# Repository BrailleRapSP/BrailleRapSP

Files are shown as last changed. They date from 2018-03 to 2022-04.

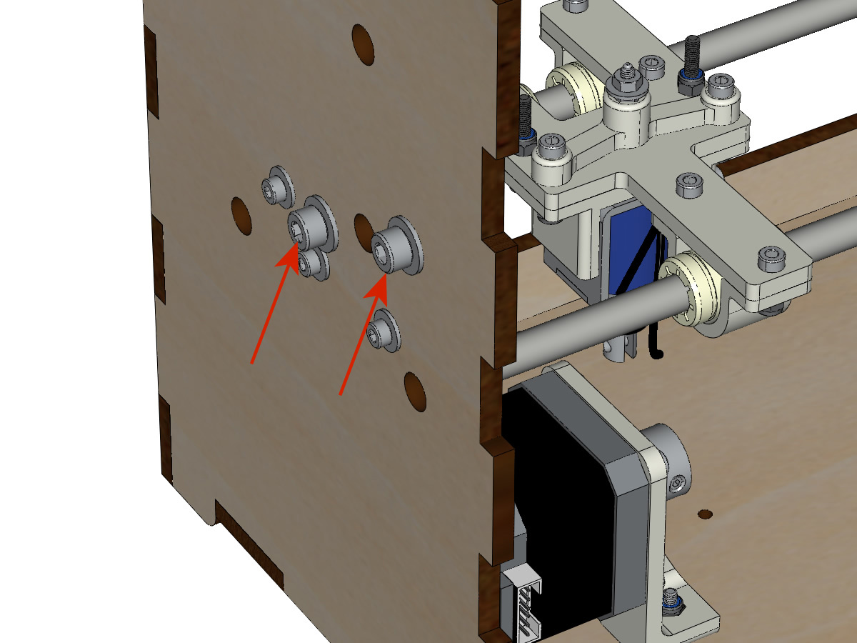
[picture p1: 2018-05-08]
docs/IMG/BrailleRAP-V5.68.jpg

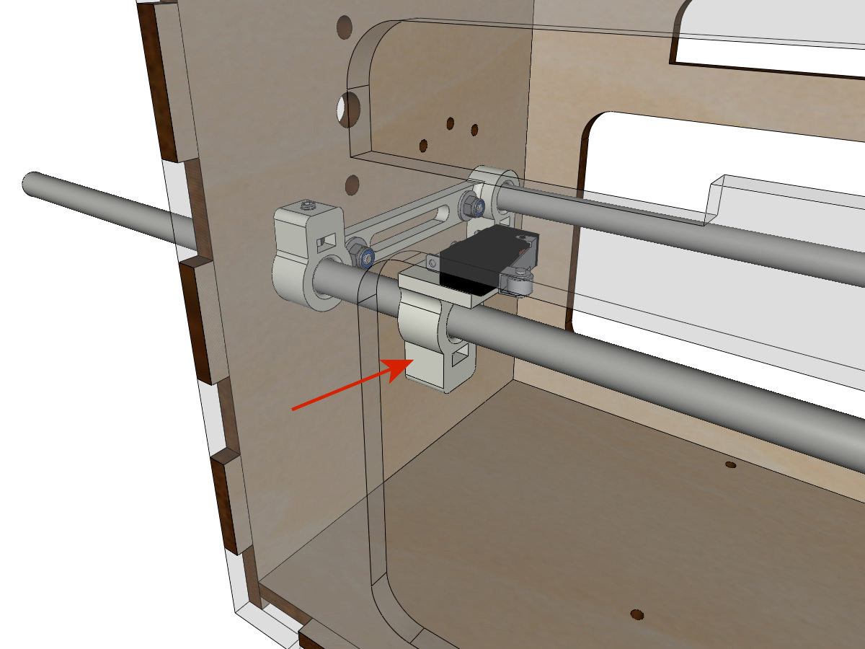
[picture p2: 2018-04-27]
docs/IMG/BrailleRAP-V5.52.jpg

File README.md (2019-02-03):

# BrailleRapSP

Embosseuse Braille Open Source

La documentation complete est disponible ici http://braillerapsp.readthedocs.io/fr/latest/index.html

voir egalement http://www.braillerap.com

==========================================================================

Open Source Braille embosser

the full documentation is available here https://braillerapsp-en.readthedocs.io/en/latest/index.html

BrailleRapSP also have a website http://www.braillerap.com

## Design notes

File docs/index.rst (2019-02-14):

.. BrailleRap-SP documentation master file, created by
   sphinx-quickstart on Mon Mar  5 11:31:40 2018.
   You can adapt this file completely to your liking, but it should at least
   contain the root `toctree` directive.

Bienvenue sur la documentation BrailleRAP-SP
============================================

.. image :: ./IMG/brailleRAP_couv.jpg 
  :width: 400px
  :align: center

Contenu:

.. toctree::
   :maxdepth: 3

   history
   licence
   bom
   assemblage
   marlin
   firstembossingpage
   
.. index:: history, licence, bom, marlin, assemblage, firstembossingpage

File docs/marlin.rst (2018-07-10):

Marlin Firmware pour cartes Ramps ou compatibles
================================================

.. Note:: Le firmware Marlin est utilisé pour contrôler l'embosseuse Braille. Nous utilisons la configuration CNC pour contrôler l'électro-aimant avec les commandes associées au moteur de CNC / stylo / laser (GCODE M3 et M4)

Configuration Marlin
-------------------

in configuration.h 

Motherboard configuration ::

   #ifndef MOTHERBOARD
     //#define MOTHERBOARD BOARD_RAMPS_14_EFB
     #define MOTHERBOARD BOARD_RAMPS_14_SF
   #endif

Spindle / laser / pen configuration ::

   // BRAILLE RAP CONFIG
   #define SPINDLE_LASER_ENABLE
   #define SPINDLE_LASER_ENABLE_PIN  RAMPS_D8_PIN      // !!! for BED MOSFET
   #define SPINDLE_LASER_PWM_PIN     RAMPS_D10_PIN     // !!! for E0 MOSFET 
   #define SPINDLE_DIR_PIN           5                 // pin servo

Endstop configuration ::

   // Mechanical endstop with COM to ground and NC to Signal uses "false" here (most common setup).
   #define X_MIN_ENDSTOP_INVERTING false // set to true to invert the logic of the endstop.
   #define Y_MIN_ENDSTOP_INVERTING false // set to true to invert the logic of the endstop.
   #define Z_MIN_ENDSTOP_INVERTING false // set to true to invert the logic of the endstop.
   #define X_MAX_ENDSTOP_INVERTING false // set to true to invert the logic of the endstop.
   #define Y_MAX_ENDSTOP_INVERTING false // set to true to invert the logic of the endstop.
   #define Z_MAX_ENDSTOP_INVERTING false // set to true to invert the logic of the endstop.
   #define Z_MIN_PROBE_ENDSTOP_INVERTING false // set to true to invert the logic of the probe.

Motor step / mm ::

   #define DEFAULT_AXIS_STEPS_PER_UNIT   { 80, 46, 4000, 500 }

Max feedrate ::

   #define DEFAULT_MAX_FEEDRATE          { 300, 300, 5, 25 }

Acceleration ::

   #define DEFAULT_MAX_ACCELERATION      { 1500, 1500, 100, 10000 }

   #define DEFAULT_ACCELERATION          1500    // X, Y, Z and E acceleration for printing moves
   #define DEFAULT_RETRACT_ACCELERATION  1500    // E acceleration for retracts
   #define DEFAULT_TRAVEL_ACCELERATION   1500    // X, Y, Z acceleration for travel (non printing) moves

Jerk ::

   #define DEFAULT_XJERK                 5.0
   #define DEFAULT_YJERK                 5.0
   #define DEFAULT_ZJERK                 0.3
   #define DEFAULT_EJERK                 5.0

Dans la version présente sur le github du projet BrailleRap-SP, d'autres fichiers ont été modifiés pour gérer l'alimentation du papier avec le fin de course de l'axe Y.

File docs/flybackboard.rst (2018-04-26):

PCB diode de roue libre 
=======================

Introduction
------------

.. Important:: Nous utilisons le connecteur de bed pour contrôler l'electro-aimant (comme on pourrait le faire avec une tête de CNC piloter par une carte RAMPS). Les electro-aimant sont des composants disposant d'une bobine, vous **devez absolument** utiliser une diode de roue libre entre le connecteur de Bed et le connecteur de l'electro-aimant pour protéger la carte RAMPS.

Schemas
-------

.. image :: ./IMG/flyback.png
    :align: center
	
.. image :: ./IMG/flyback_schema.png
    :align: center

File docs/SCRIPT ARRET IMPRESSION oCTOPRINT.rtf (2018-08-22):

M104 S0 ;extruder heater off
M140 S0 ;heated bed heater off (if you have it)
G91 ;relative positioning
G1 E-1 F300 ;retract the filament a bit before lifting the nozzle, to release some of the pressure
G1 Z+0.5 E-5 X-20 Y-20 F5000 ;move Z up a bit and retract filament even more
G28 X0 Y0 ;move X/Y to min endstops, so the head is out of the way
M84 ;steppers off
G90 ;absolute positioning
M107 ;start with the fan off
;{profile_string}

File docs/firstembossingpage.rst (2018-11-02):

Embosser votre première page de Braille
=======================================

BrailleRapSP est est machine qui se pilote en G-CODE, pour embosser du braille il faut tout d'abord traduire le texte en Braille.
Il existe 2 solutions pour traduire le Braille :
L'application BrailleRap en ligne https://crocsg.github.io/BrailleRap/
L'application NatBraille http://natbraille.free.fr 

Utilisation de l'application BrailleRap
---------------------------------------

Aller sur la page https://crocsg.github.io/BrailleRap/

.. image :: ./IMG/braillerapapp.png
       :align: center
Entrer votre texte à l'endroit indiqué, et télécharger ensuite le fichier GCODE contenant les instructions pour l'embosseuse

.. image :: ./IMG/braillerapapp_download.png
       :align: center

Vous pouvez ensuite utiliser un logiciel comme **cura** ou **pronterface** pour envoyer le fichier GCODE à l'imprimante

Configuration NatBraille
------------------------

Compiler les programmes dans le repertoire NatBrailleTools du projet

Dans les options générales NatBraille, utiliser **TbFr2007** pour la table braille, Encodage document noir **Automtique**, Encodage document braille **Windows1252**

.. image :: ./IMG/natbraille.png
       :align: center

Dans les options d'embossage, utiliser **TbFr2007** pour la table braille pour l'embossage

Activer l'option **utiliser une commande systeme pour l'embossage**

le paramêtre  pour commande d'impression est : **java -jar d:\\usr\\home\\logger\\BrailleLogger.jar $f | java -jar d:\\usr\\home\\logger\\gcodestreamer.jar COM4 250000**
en modifiant eventuellement les repertoires d'installation des programmes
COM4 est le port serie utilisé pour communiquer avec l'imprimante

.. image :: ./IMG/natbrailleembossig.png
       :align: center

Dans les options de mise en page, indiquer 31 et 26 dans le nombre de caracter par ligne et le nombre de lignes par page

.. image :: ./IMG/natbraille_page.png
       :align: center

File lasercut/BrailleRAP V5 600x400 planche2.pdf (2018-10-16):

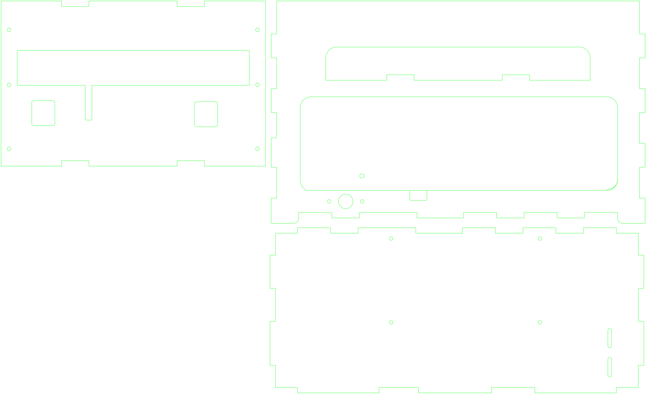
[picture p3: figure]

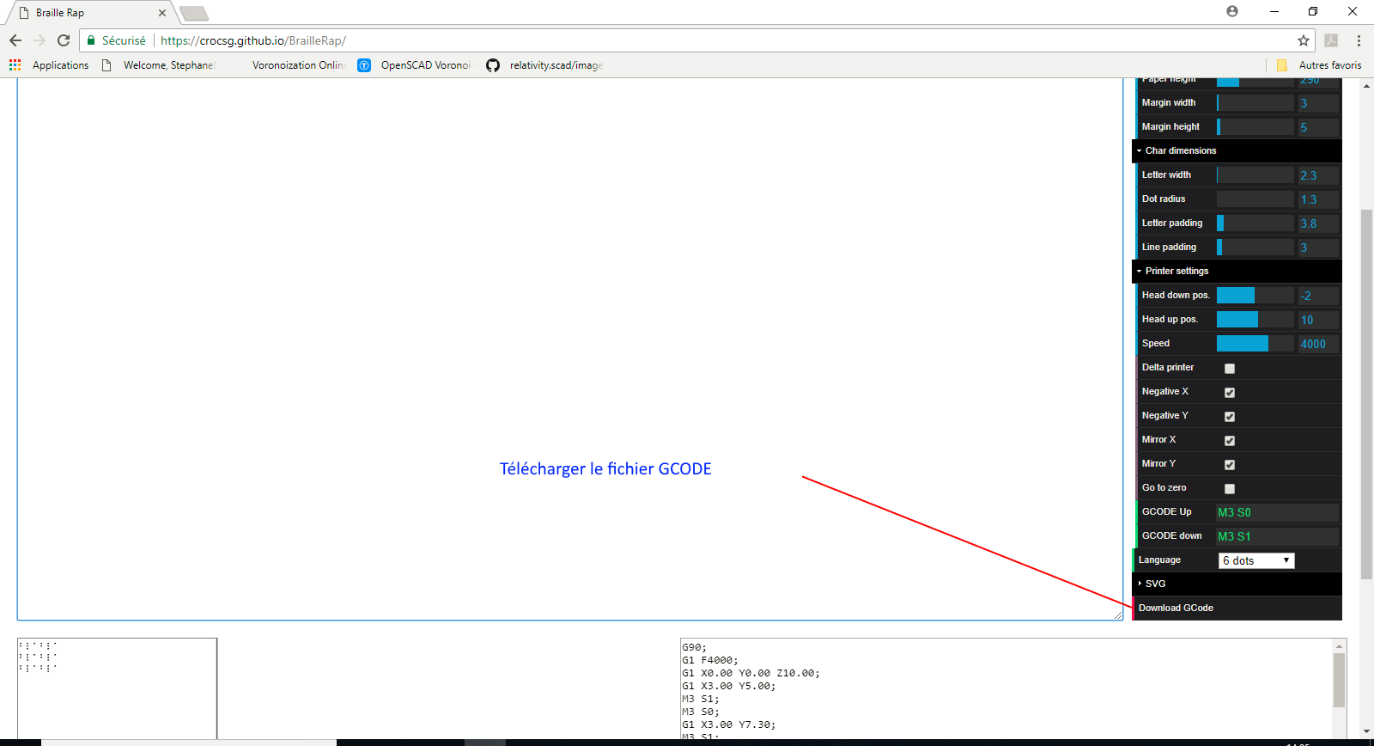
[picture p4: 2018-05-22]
docs/IMG/braillerapapp_download.png

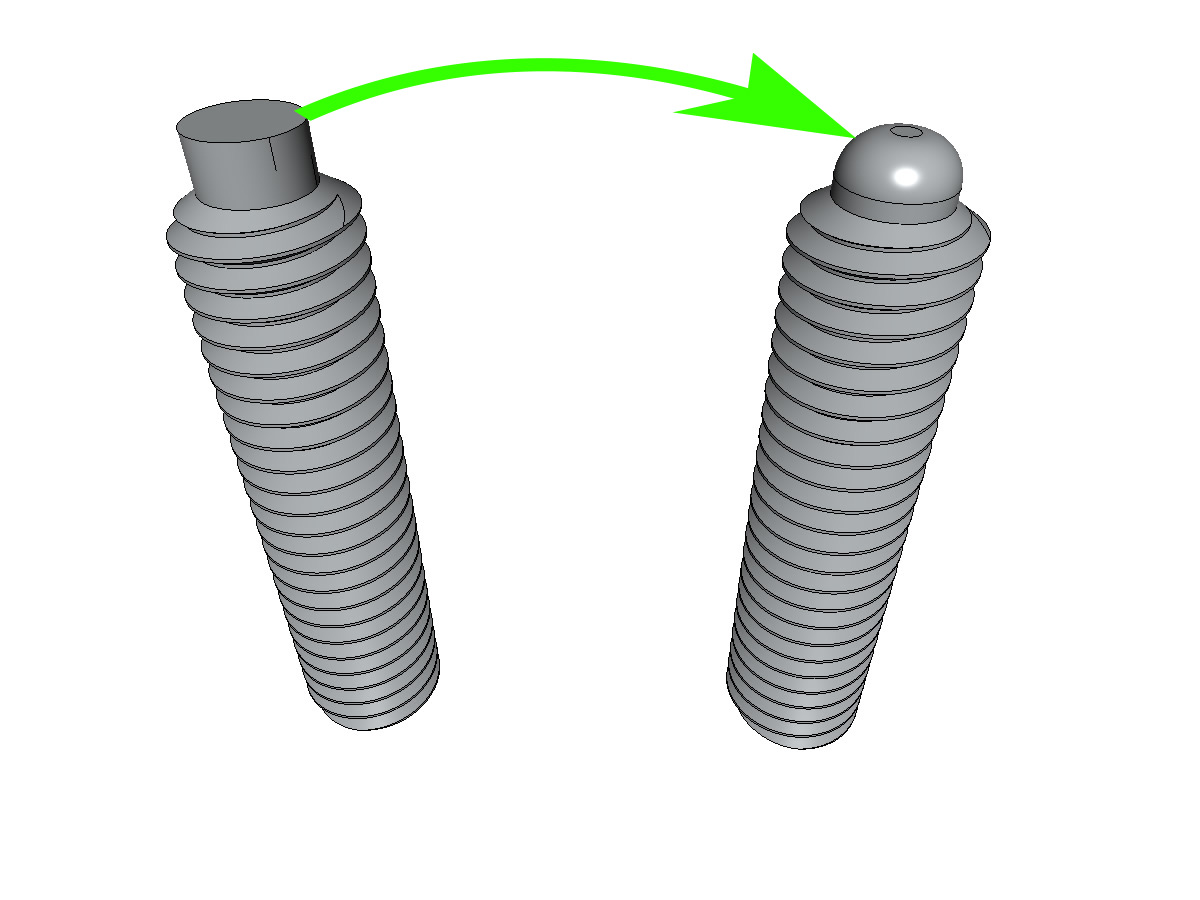
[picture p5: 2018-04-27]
docs/IMG/BrailleRAP-V5.56.jpg

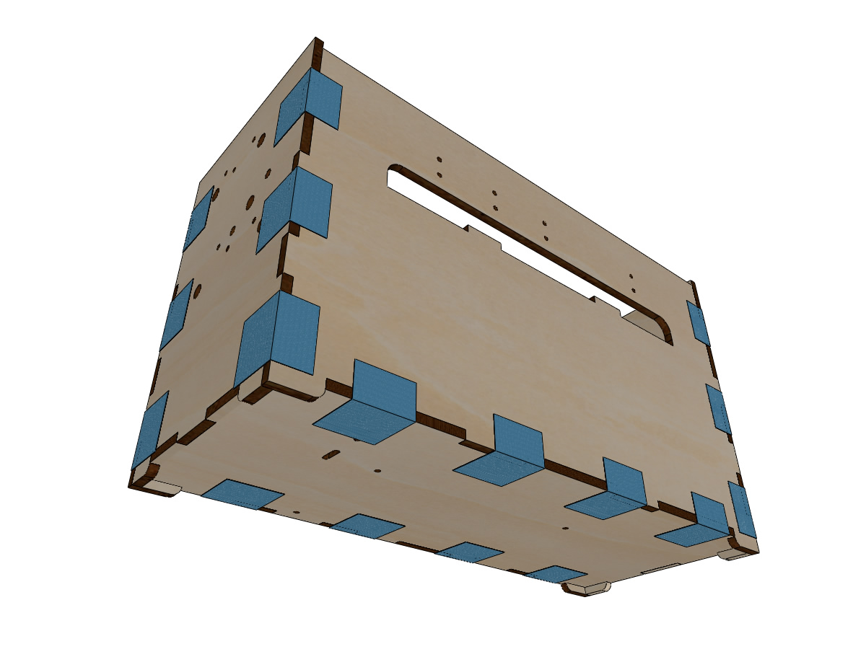
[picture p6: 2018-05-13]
docs/IMG/BrailleRAP-V5.01.jpg

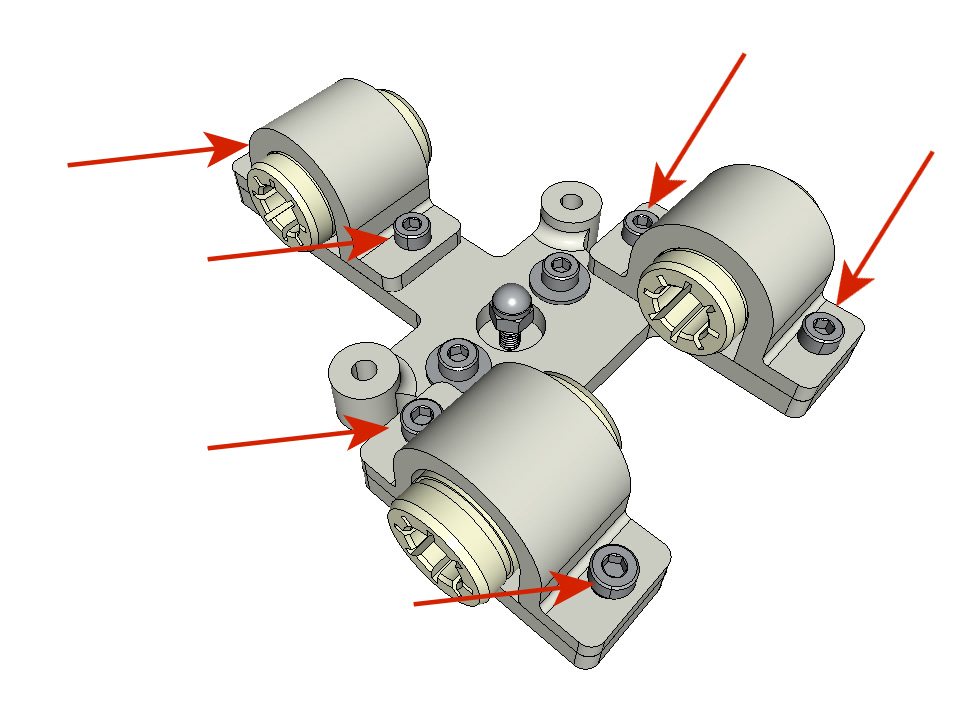
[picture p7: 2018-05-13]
docs/IMG/BrailleRAP-V5.85.jpg

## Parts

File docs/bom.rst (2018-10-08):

Liste du matériel
================

Découpe laser
-------------
2 planches de contreplaqué 5mm en 600mm x 400mm.

Les fichiers au format dxf sont disponibles ici : https://github.com/BrailleRapSP/BrailleRapSP/tree/master/lasercut

Pièces imprimées
-------------
Toutes les pièces sont imprimées en ABS, 50% de remplissage, 3 périmètres extérieurs. Nous utilisons le filament eSun ABS Natural.

Ajouter le lien pour le téléchargement de STL

Pièces mécaniques
----------------

=== =========================================
Qty Type
=== =========================================
4   Rail de guidage linéaire ( diamètre 8mm ) 330 mm length
1   Rail de guidage linéaire ( diamètre 8mm ) 365 mm length
1   Rail de guidage linéaire ( diamètre 8mm ) *100 mm* length

6   RJ4JP-01-08 palier linéaire Polymer  

3   GT2 poulie 20 dents pour axe 8mm    
2   GT2 poulie libre 20 dents axe 3mm (avec roulement à billes)

2   KP08  pallier horizontal pour rail linéaire 8mm 
2   KFL08 pallier vertical pour rail linéaire 8mm 

1   Accouplement d'axe 5mm/8mm

2   Nema 17 40 N/cm avec câble

1   Courroie GT2 fermée 200 mm
2   630 mm de courroie GT2

2   Joints torique 15.1 mm diamètre intérieur 20.5 mm de diamètre extérieur (15.1 x 20.5 x 2.7)
...
=== =========================================

Electronique
------------------

=== =========================================
Qty Type
=== =========================================
1   MKS GEN 1.4 ou carte compatible Ramps 1.4 
2   drivers DRV8825 avec radiateur
1   Electro-aimant *tau-826* 12V 2A
1   1N4004  diode de roue libre ou equivalent (12V 2A)
1   Embase Alimentation jack 2.5
1   Alimentation 12v 6A 
=== =========================================

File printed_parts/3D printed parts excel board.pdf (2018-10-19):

SCROLL_wheel | 2
KP08_support | 2
IGUS_housing | 6

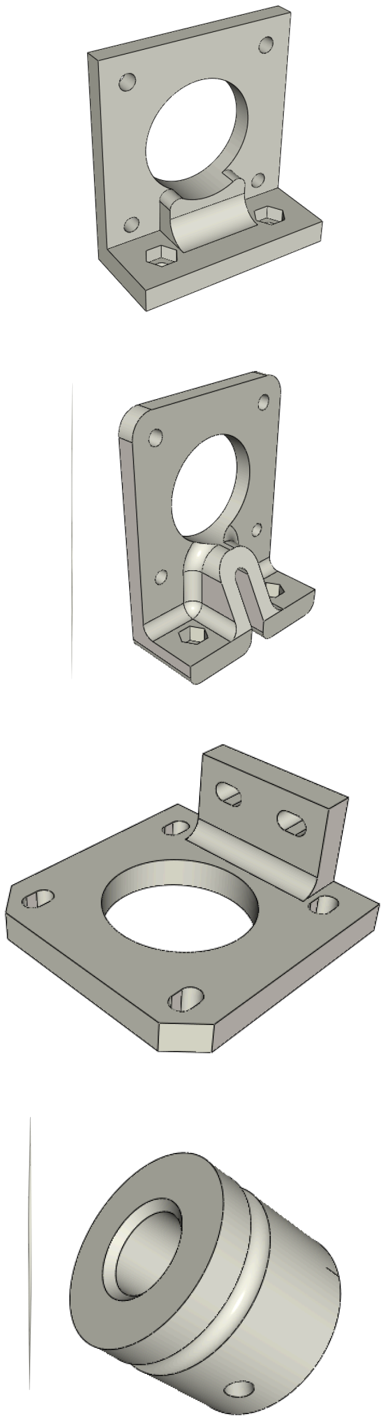
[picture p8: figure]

YMOTOR_support_220 | 1 | for 220mm GT2 timing belt
YMOTOR_support_200 | 1 | for 200mm GT2 timing belt
XMOTOR_support | 1
ROLL_joint | 2
BOTTOM_trolley | 1

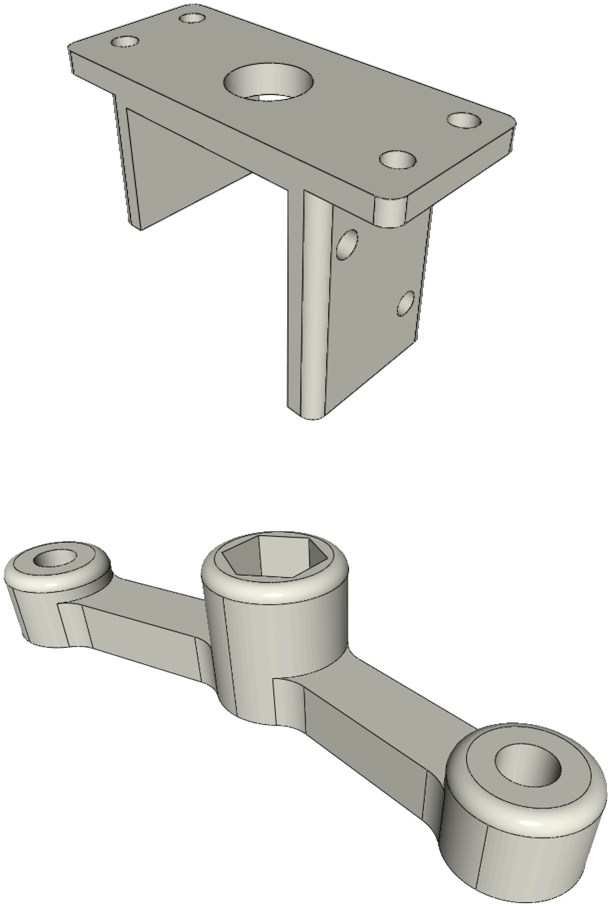
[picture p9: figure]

ELECTRO_MAGNET_housing | 1
ELECTRO_MAGNET_guide | 1
TOP_trolley | 1

FEMALE_shape | 1
TOP_AXIS_left | 1

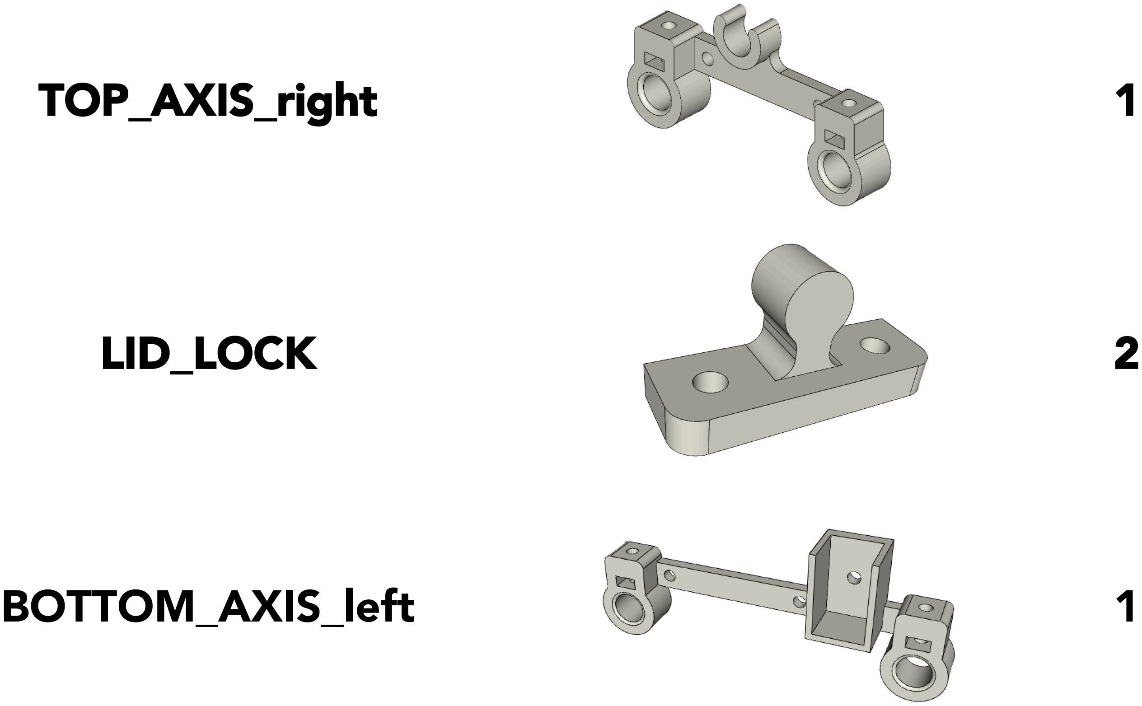
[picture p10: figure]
TOP_AXIS_right; LID_LOCK; BOTTOM_AXIS_left

BOTTOM_AXIS_right | 1
DRIVEN_PULLEY_housing | 2
PAPER_GUIDE_left | 1
PAPER_GUIDE_right | 1
SWITCH_Y_support | 1
PAPER_raiser | 2

SWITCH_X_support | 1
CLIPBOARD | 2
CLIPBOARD_WHEEL | 2
POWER_plate | 1

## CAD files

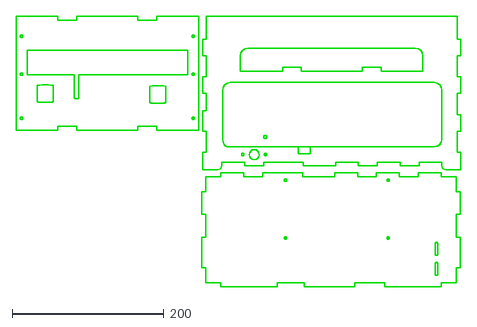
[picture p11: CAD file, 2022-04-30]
lasercut/BrailleRAP V5 600x400 planche2-r14.dxf
585.6 x 355.9

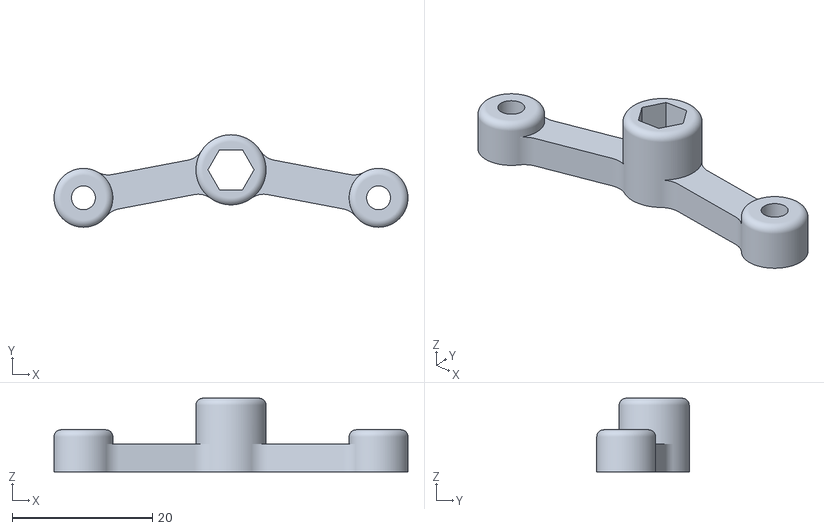
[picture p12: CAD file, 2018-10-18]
printed_parts/ELECTRO_MAGNET_guide.stl
50.5 x 13.2 x 10.5

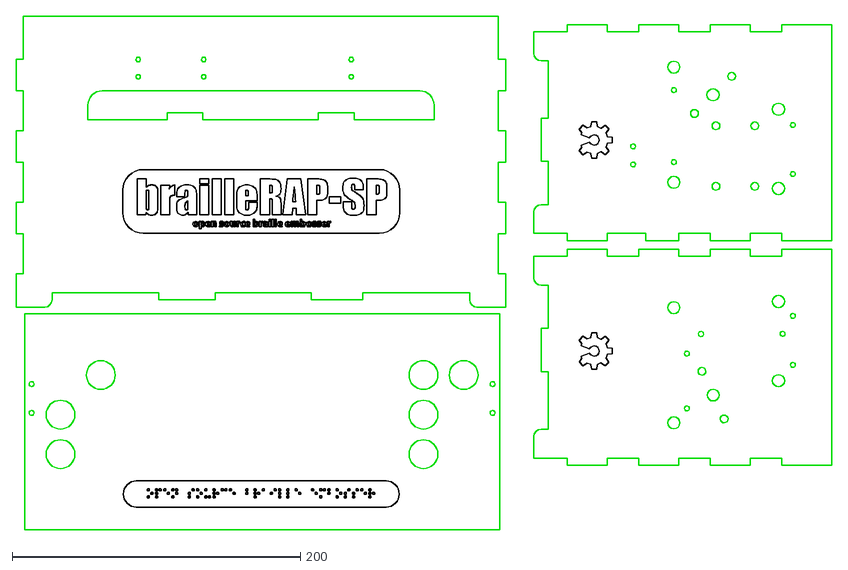
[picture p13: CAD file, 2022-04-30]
lasercut/BrailleRAP V5 600x400 planche1_r14.dxf
566.6 x 356.7

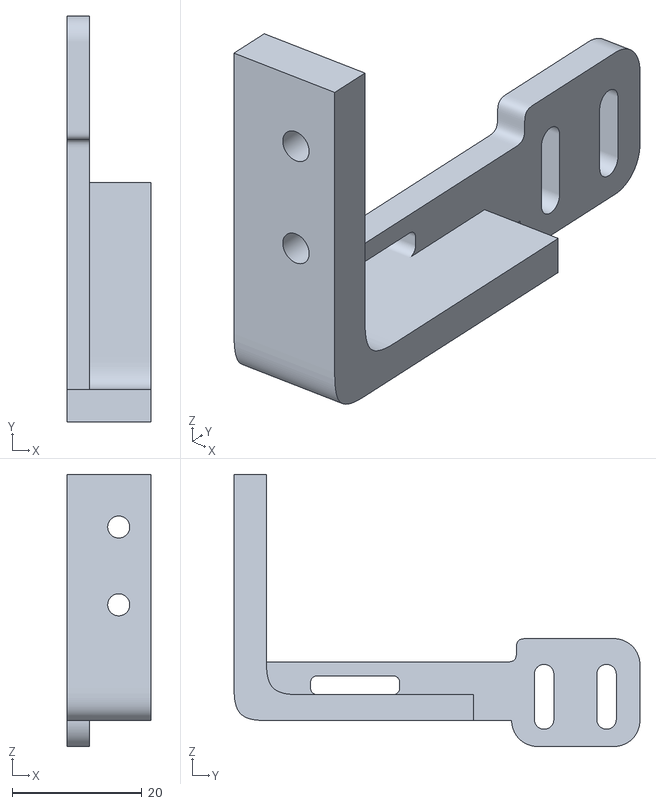
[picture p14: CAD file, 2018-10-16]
printed_parts/SWITCH_Y_support.stl
13.0 x 62.6 x 42.0

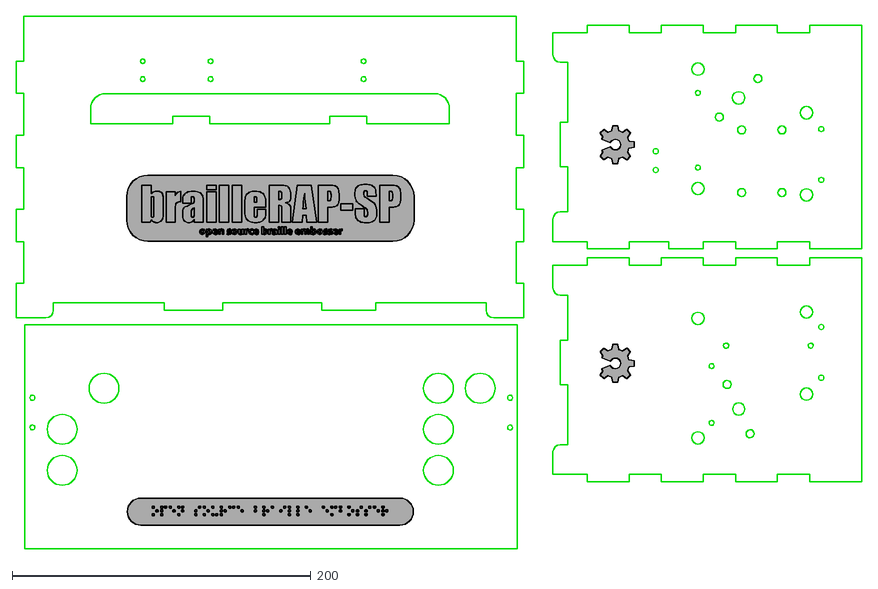
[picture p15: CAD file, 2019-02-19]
lasercut/BrailleRAP V5 600x400 planche1.dxf
566.6 x 356.7

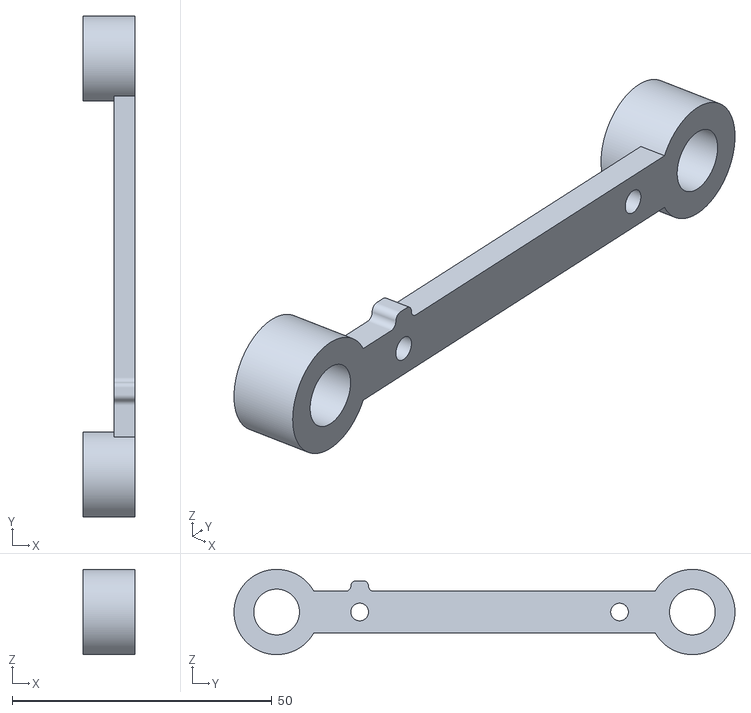
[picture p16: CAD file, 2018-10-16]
printed_parts/BOTTOM_AXIS_right.stl
10.0 x 96.4 x 16.4

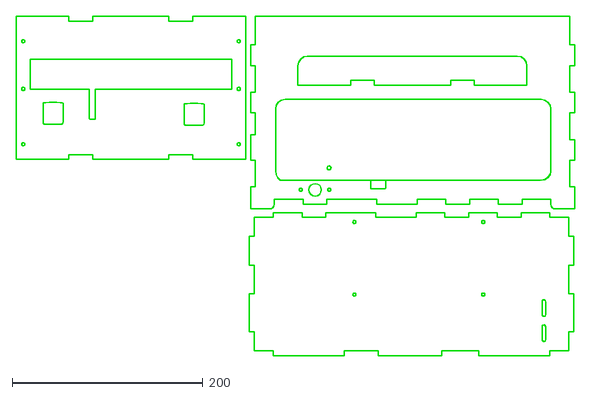
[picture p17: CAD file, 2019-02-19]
lasercut/BrailleRAP V5 600x400 planche2.dxf
585.6 x 355.9

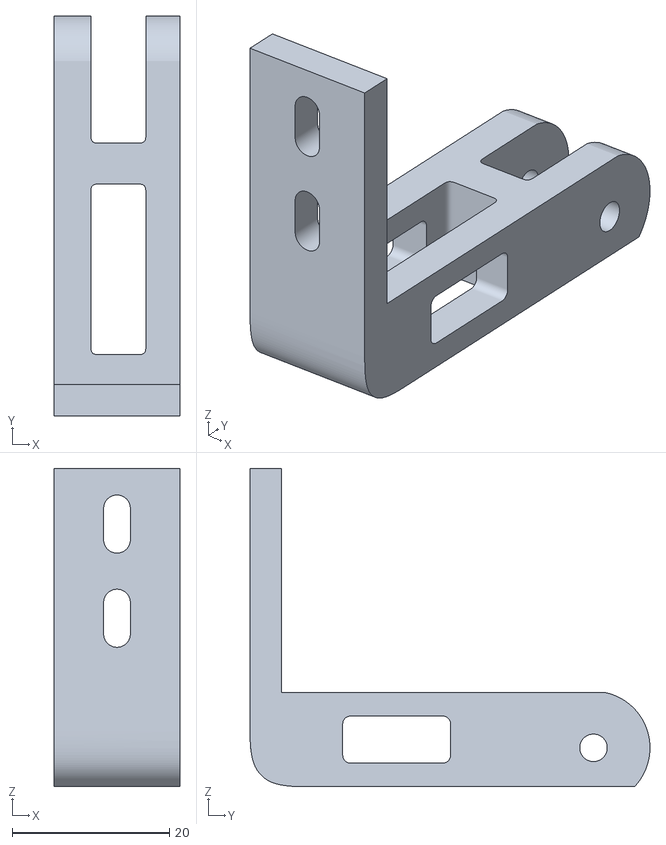
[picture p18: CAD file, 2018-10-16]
printed_parts/CLIPBOARD.stl
16.0 x 51.0 x 40.6

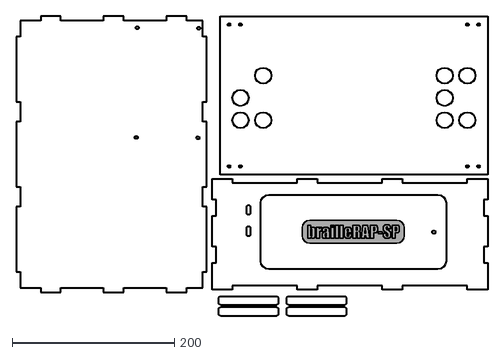
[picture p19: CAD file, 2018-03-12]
lasercut/PLANCHE 1.dxf
581.6 x 369.0

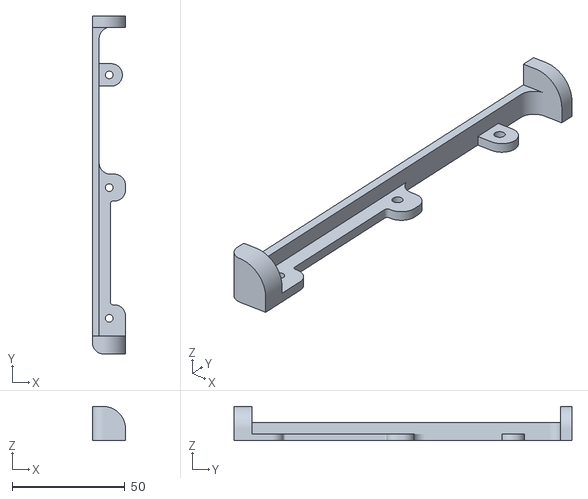
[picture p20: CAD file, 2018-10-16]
printed_parts/PAPER_GUIDE_right.stl
14.7 x 150.0 x 15.2

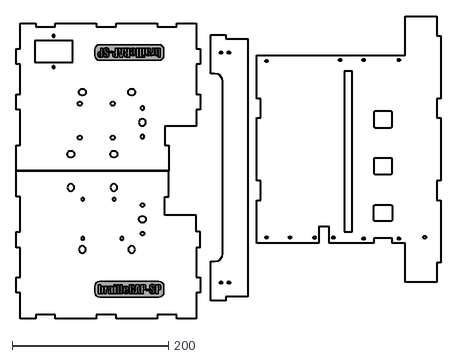
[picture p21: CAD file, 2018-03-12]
lasercut/PLANCHE 2.dxf
542.5 x 386.6

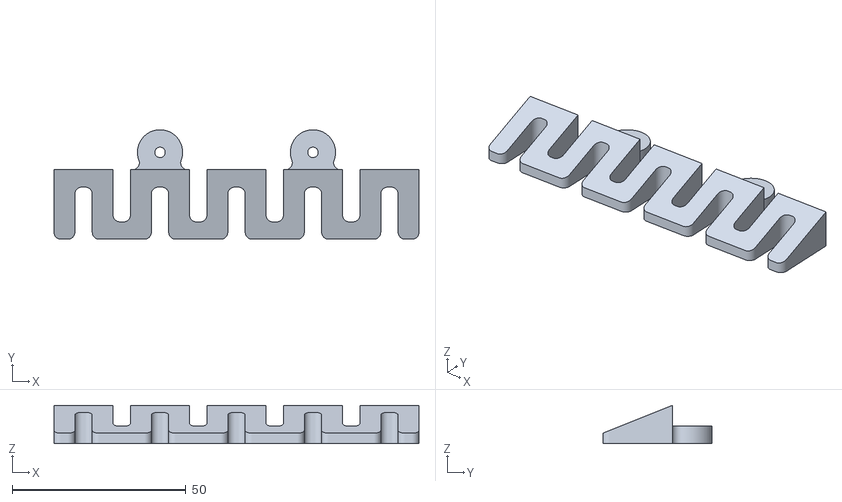
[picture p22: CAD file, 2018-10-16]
printed_parts/PAPER_RAISER.stl
105.0 x 31.5 x 11.0

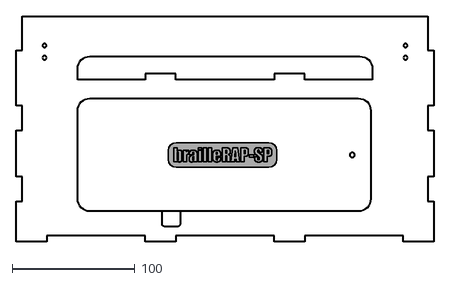
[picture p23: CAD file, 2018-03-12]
lasercut/PLANCHE 3.dxf
340.0 x 184.0

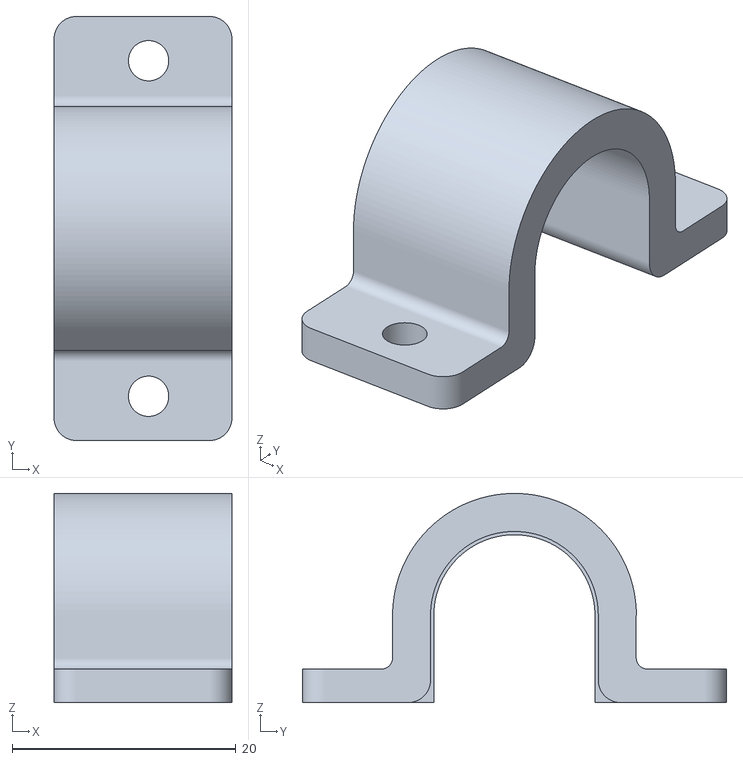
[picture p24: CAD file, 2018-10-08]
printed_parts/IGUS_housing.stl
15.9 x 37.9 x 18.7

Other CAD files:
printed_parts/PAPER_GUIDE_left.stl
printed_parts/ROLL_joint.stl
printed_parts/CLIPBOARD_WHEEL.stl
printed_parts/BOTTOM_trolley.stl
printed_parts/BOTTOM_AXIS_left.stl
printed_parts/DRIVEN_PULLEY_housing.stl
printed_parts/ELECTRO_MAGNET_housing.stl
printed_parts/ENDSTOPX_support.stl
printed_parts/FEMALE_shape.stl
printed_parts/IGUS_housing_2.stl
printed_parts/KFL8_support.stl
printed_parts/KP08_support.stl
printed_parts/LID_LOCK.stl
printed_parts/POWER_plate.stl
printed_parts/SCROLL_wheel.stl
printed_parts/SWITCH_X_support.stl
printed_parts/TOP_AXIS.stl
printed_parts/TOP_AXIS_left.stl
printed_parts/TOP_AXIS_right.stl
printed_parts/TOP_trolley.stl
printed_parts/XMOTOR_support.stl
printed_parts/YMOTOR_support_200.stl

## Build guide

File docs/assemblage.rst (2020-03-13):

Manuel de montage BrailleRAP-SP
===============================

Collage de la caisse en bois
-----------------------------

Matériel:

    * FACE (contre-plaqué de 5mm découpé au laser).
    * BACK (contre-plaqué de 5mm découpé au laser).
    * BOTTOM (contre-plaqué de 5mm découpé au laser).
    * LEFT_SIDE (contre-plaqué de 5mm découpé au laser).
    * RIGHT_SIDE (contre-plaqué de 5mm découpé au laser).
    * Colle à bois.
    * Scotch de peintre.

* Préparer le 5 éléments : FACE, BACK, LEFT_SIDE, RIGHT_SIDE et BOTTOM.

.. image :: ./IMG/BrailleRAP-V5.02.1.jpg
       :align: center

* Encoller les encoches, assembler les 5 parties et les maintenir en place avec du scotch de peintre le temps du séchage préconisé par le fabricant.

.. image :: ./IMG/BrailleRAP-V5.01.jpg
       :align: center

Collage des bloqueurs de trappe
-------------------------------

Matériel:

    * Caisse bois assemblée.
    * 3 disques en bois récupérés de la découpe laser du couvercle.
    * Colle à bois.

* Coller les 3 disques de bois sur la façade arrière à l'intérieur de la caisse. Ces disques maintiendront la trappe d'accès à l'intérieur de la machine.

.. image :: ./IMG/BrailleRAP-V5.01.2.jpg
       :align: center

Préparation du pointeau mâle
-----------------------------

Matériel :

    * 1 lime pour métaux ou de la toile émeri ou une Dremel
    * 1 vis sans tête M3-16 bout téton

* Limer l'arête du téton afin d’obtenir un profil approchant celui illustré.

.. image :: ./IMG/BrailleRAP-V5.56.jpg
       :align: center

Moteur Y
---------

Matériel :

    * **Pièce(s) imprimée(s) en 3D** :  YMOTOR_support_200 ou YMOTOR_support_220 (selon la longueur de la courroie fermée GT2)
    * 1 moteur Nema 17
    * 1 poulie GT2 20 dents bore 5mm
    * 4 vis M3-8
    * 2 écrous NYL M3
    * 2 vis M3-12
    * 2 rondelles M3 larges

* Visser la poulie sur l’arbre du moteur en s’assurant qu’au moins une des deux vis soit en face du méplat de l’axe du moteur et que les dents de la poulie soient orientées vers le moteur.

.. image :: ./IMG/BrailleRAP-V5.03.jpg
       :align: center

* Monter le moteur sur son support avec les 4 vis M3-8 en s'assurant que le connecteur soit dans la position correspondante à l'illustration.

.. image :: ./IMG/BrailleRAP-V5.04.jpg
       :align: center

.. ATTENTION:: L'illustration montre un support moteur prévu pour une courroie de 200mm mais le montage est le même avec un support moteur prévu pour une courroie de 220mm.

* Introduire les écrous NYL M3 dans le support moteur.

.. image :: ./IMG/BrailleRAP-V5.05.jpg
       :align: center

* Introduire les vis et les rondelles par l’extérieur et visser le support sur la caisse afin qu’il puisse encore coulisser dans les trous oblongs.

.. image :: ./IMG/BrailleRAP-V5.06.1.jpg
       :align: center

.. image :: ./IMG/BrailleRAP-V5.07.1.jpg
       :align: center

Préparation de supports d’axes
--------------------------------

  * **Pièce(s) imprimée(s) en 3D** : BOTTOM_AXIS_left
  * **Pièce(s) imprimée(s) en 3D** : BOTTOM_AXIS_right
  * **Pièce(s) imprimée(s) en 3D** : TOP_AXIS_left
  * **Pièce(s) imprimée(s) en 3D** : TOP_AXIS_right
  * 1 foret de 8mm
  * 8 écrous M3
  * 8 vis M3-12

.. ATTENTION:: Selon la qualité d’impression des pièces en plastique, veiller à ce que les barres de 8mm puissent coulisser facilement dans leurs logements. Le cas échéant, percer le trou avec un foret de 8.

* Pour chacune des 4 pièces, introduire un écrou M3 dans les trous rectangulaires. Visser les vis M3-12.

.. image :: ./IMG/BrailleRAP-V5.09.1.jpg
       :align: center

* L’extrémité de la vis ne doit pas dépasser dans le passage des barres de Ø 8mm.

.. image :: ./IMG/BrailleRAP-V5.10.jpg
       :align: center

.. image :: ./IMG/BrailleRAP-V5.11.jpg
       :align: center

Fixation des supports GAUCHES des axes
----------------------------------------------

Matériel :

  * **Pièce(s) imprimée(s) en 3D** :  BOTTOM_AXIS_left préparé avec écrou et vis sans tête (cf Préparation de supports d’axes)
  * **Pièce(s) imprimée(s) en 3D** :  TOP_AXIS_left préparé avec écrou et vis sans tête (cf Préparation de supports d’axes)

  * 4 vis BTR M3-14
  * 4 rondelles M3 larges
  * 4 écrous NYL M3

* Fixer les supports d’axe sur la caisse le BOTTOM_AXIS_left et TOP_AXIS_left à gauche en laissant un peu de jeu (vis+rondelle à l'extérieur et écrou à l'intérieur). Les vis seront serrées quand l'ensemble sera en place.

.. image :: ./IMG/BrailleRAP-V5.12.1.jpg
       :align: center

.. image :: ./IMG/BrailleRAP-V5.12.2.jpg
       :align: center

Fixation des supports DROITS des axes
-------------------------------------

Matériel :

  * **Pièce(s) imprimée(s) en 3D** :  BOTTOM_AXIS_right
  * **Pièce(s) imprimée(s) en 3D** :  TOP_AXIS_right préparé avec écrou et vis sans tête (cf Préparation de supports d’axes)
  * 4 vis BTR M3-14
  * 4 rondelles M3 larges
  * 4 écrous NYL M3

* Fixer les supports d’axe sur la caisse le BOTTOM_AXIS_right (attention à la position du repère) et TOP_AXIS_right à droite en laissant un peu de jeu (vis+rondelle à l'extérieur et écrou à l'intérieur). Les vis seront serrées quand l'ensemble sera en place.

.. image :: ./IMG/BrailleRAP-V5.12.3.jpg
       :align: center

.. image :: ./IMG/BrailleRAP-V5.12.4.jpg
       :align: center

Fixation des tendeurs de courroie
----------------------------------------------

Matériel :

  * **Pièce(s) imprimée(s) en 3D** :  2 x DRIVEN_PULLEY_housing
  * 2 vis BTR M3-20
  * 2 rondelles M3 larges
  * 2 écrous NYL M3

* Insérer un écrou M3 NYL dans son logement et fixer les DRIVEN_PULLEY_housing avec une vis M3-20 et une rondelle.

.. image :: ./IMG/BrailleRAP-V5.44.jpg
       :align: center

.. image :: ./IMG/BrailleRAP-V5.13.3.jpg
       :align: center

.. image :: ./IMG/BrailleRAP-V5.13.5.jpg
       :align: center

* Laisser un jeu de ±5mm.

.. image :: ./IMG/BrailleRAP-V5.13.4.jpg
       :align: center

Pose des poulies libres de renvoi
----------------------------------------------

Matériel :

  * 2 poulies libres 20 dents bore 3mm
  * 2 vis BTR M3-25
  * 2 écrous NYL M3

* Commencer par insérer la poulie puis la vis M3-25. Visser avec un écrou M3 NYL sans trop serrer.

.. image :: ./IMG/BrailleRAP-V5.13.6.jpg
       :align: center

Montage de l'interrupteur de fin de course X
---------------------------------------------

Matériel :

  * **Pièce(s) imprimée(s) en 3D** : SWITCH_X_support
  * 1 interrupteur fin de course câblé (cf câblage des interrupteurs fin de course)
  * 1 vis sans tête M3-8
  * 1 écrou M3
  * 2 vis M2.5-14 **Michel, on t'a mis des M2.5-14 ;)**
  * 2 écrous M2.5

.. Note:: Changer l'image avec support interrupteur (nouveau modèle).

* Introduire un écrou M3 et visser une vis sans tête M3-8.

.. image :: ./IMG/BrailleRAP-V5.57.jpg
       :align: center

* Visser l'interrupteur fin de course sur son support (SWITCH_X_support) à l'aide des vis M2.5-12 et des écrous M2.5.

.. Note:: L'interrupteur fin de course est représenté non câblé mais il devra être câblé avant le montage.

.. image :: ./IMG/BrailleRAP-V5.58.jpg
       :align: center

Préparation de l’électro-aimant
--------------------------------

Matériel :

  * 1 électro-aimant
  * 1 entretoise de 18mm
  * 1 vis sans tête M3-12 pointeau limée (cf Préparation du pointeau mâle)
  * 1 écrou M3
  * 1 rondelle M3 moyenne

* Visser l’entretoise à fond sur l’électro-aimant.

.. image :: ./IMG/BrailleRAP-V5.16.jpg
       :align: center

* Visser la vis M3-12 pointeau limée en la laissant dépasser de ± 6mm de l’entretoise.

.. image :: ./IMG/BrailleRAP-V5.17.jpg
       :align: center

Montage du chariot bas (étape 1)
---------------------------------

Matériel :

  * Ensemble électro-aimant pré assemblé (cf Préparation de l’électro-aimant)
  * **Pièce(s) imprimée(s) en 3D** : BOTTOM_trolley
  * **Pièce(s) imprimée(s) en 3D** : ELECTRO_MAGNET_housing
  * **Pièce(s) imprimée(s) en 3D** : ELECTRO_MAGNET_guide
  * **Pièce(s) imprimée(s) en 3D** : 3 X IGUS_housing
  * 2 vis M3-8
  * 3 IGUS
  * 6 vis M3-12
  * 10 écrous M3 NYL
  * 2 vis M3-18
  * 2 vis M3-20

* Fixer l’électro-aimant sur son support avec les 2 vis M3-8.

.. ATTENTION:: Respecter le côté de sortie des fils.

.. image :: ./IMG/BrailleRAP-V5.19.jpg
       :align: center

* Introduire les 3 IGUS dans leur logement (IGUS_housing).

.. ATTENTION:: Respecter le côté du rainurage.

.. image :: ./IMG/BrailleRAP-V5.14.1.jpg
       :align: center

* Assembler les 3 logements + IGUS + BOTTOM_trolley avec les 6 vis M3-12 et les 6 écrous M3 NYL.

.. ATTENTION:: Ne pas serrer les vis à fond. Elles seront serrées quand le chariot sera en place sur ses rails de guidage.

.. image :: ./IMG/BrailleRAP-V5.14.2.jpg
       :align: center

* Assembler l'électro-aimant (préalablement monté dans son logement) sous le BOTTOM_trolley et le ELECTRO_MAGNET_guide avec les deux vis M3-18 et 2 écrous M3 NYL.

.. ATTENTION:: Selon la qualité de l'impression, il sera peut-être nécessaire de limer le logement de l'entretoise.

.. image :: ./IMG/BrailleRAP-V5.14.3.jpg
       :align: center

* Visser les deux vis M3-20 (qui retiendront la courroie) et 2 écrous M3 NYL avec la tête de vis en dessous.

.. image :: ./IMG/BrailleRAP-V5.14.4.jpg
       :align: center

* Mettre une rondelle et serrer le contre écrou M3 en veillant à ce que la vis pointeau ne se visse pas en même temps dans l’entretoise. La rondelle empêche le contre écrou de se coincer dans le guide de l’entretoise.

.. image :: ./IMG/BrailleRAP-V5.14.5.jpg
       :align: center

Montage du chariot bas (étape 2)
---------------------------------

Matériel :

  * 2 barres lisses Ø8mm, longueur : 330mm

.. NOTE:: Nous n'avons pas représenté la façade pour des raisons de lisibilité.

* Enfiler les barres à mi-course par l’extérieur de la caisse.

.. image :: ./IMG/BrailleRAP-V5.51.1.jpg
       :align: center

* Enfiler le fin de course et son support sur la barre Ø8mm côté face arrière.

.. image :: ./IMG/BrailleRAP-V5.51.2.jpg
       :align: center

.. NOTE:: La vis du support de l'interrupteur sera serrée plus tard lors du réglage.

* Enfiler le chariot bas sur les barres lisses.

.. image :: ./IMG/BrailleRAP-V5.51.3.jpg
       :align: center

* Terminer d’enfiler les barres (les barres ne doivent pas dépasser dans le bois de la caisse).
* Serrer les 4 vis des supports d’axes sur la caisse (2 sur le côté gauche et 2 sur le côté droit) et les 4 vis sans tête des supports des axes suffisamment pour que les axes ne coulissent dans leurs logements.

.. image :: ./IMG/BrailleRAP-V5.51.4.jpg
       :align: center

* Serrer les 6 vis des IGUS_housing petit à petit en s'assurant que le chariot coulisse bien sur les axes.

.. image :: ./IMG/BrailleRAP-V5.51.6.jpg
       :align: center

Montage de l’axe vertical (étape 1)
------------------------------------

Matériel :

  * **Pièce(s) imprimée(s) en 3D** : XMOTOR_support
  * 1 moteur NEMA 17
  * 4 vis M3-8
  * 2 vis M3-16
  * 2 écrous M3 NYL
  * 4 rondelles M3 grandes

* Visser le moteur sur son support en laissant un peu de jeu et en respectant la position du connecteur.

.. Note:: Le jeu permettra ensuite d'aligner l'arbre du moteur avec l'axe vertical.

.. image :: ./IMG/BrailleRAP-V5.31.jpg
       :align: center

* Visser l’ensemble moteur/support sur la caisse avec les 2 vis M3-16 en laissant du jeu.

.. image :: ./IMG/BrailleRAP-V5.32.1.jpg
       :align: center

.. image :: ./IMG/BrailleRAP-V5.33.1.jpg
       :align: center

Montage de l’axe vertical (étape 2)
------------------------------------

Matériel :

  * **Pièce(s) imprimée(s) en 3D** : 2 X KP08_support
  * 2 KP08
  * 4 vis M5-25
  * 4 rondelles M5
  * 4 écrous M5 NYL

.. NOTE:: Avant de fixer les KP08, s'assurer que les roulements sont bien alignés dans leurs logements. Il se peut qu'ils soient livrés un peu désaxés. Dans ce cas, introduire une barre Ø 8mm et l'actionner manuellement afin de les redresser.

.. image :: ./IMG/BrailleRAP-V5.40.jpg
       :align: center

* Visser les KP08_support et les KP08 sur la caisse en laissant un peu de jeu avec les vis M5-25, les rondelles M5 et les écrous M5 NYL.

.. image :: ./IMG/BrailleRAP-V5.34.1.jpg
       :align: center

* Respecter la position des bagues de serrage des KP08.

.. image :: ./IMG/BrailleRAP-V5.36.1.jpg
       :align: center

.. image :: ./IMG/BrailleRAP-V5.35.1.jpg
       :align: center

Montage de l’axe vertical (étape 3)
------------------------------------

Matériel :

  * 1 barre lisse Ø 8mm, longueur : 100mm
  * 1 Coupleur 5*8mm

* Enfiler le coupleur sur l’arbre du moteur (trou Ø 5mm en bas).

.. image :: ./IMG/BrailleRAP-V5.59.jpg
       :align: center

* Enfiler la barre lisse de 100mm depuis le haut à travers les KP08 et dans le coupleur.

.. image :: ./IMG/BrailleRAP-V5.60.1.jpg
       :align: center

* Faire tourner l’axe à la main pour s’assurer que tous les éléments sont bien alignés et que l'axe continue à tourner librement.

.. image :: ./IMG/BrailleRAP-V5.60.2.jpg
       :align: center

* Les trous du support moteur sont oblongs et permettent d'aligner le moteur avec l'axe vertical dans les 2 dimensions.
* Visser les 2 premières vis du moteur sur son support.

.. image :: ./IMG/BrailleRAP-V5.61.jpg
       :align: center

* Visser petit à petit les vis des KP08 en faisant tourner l’axe à la main.
* Visser petit à petit les vis du support moteur sur la caisse en faisant tourner l’axe à la main. **AJOUTER IMAGE**
* Retirer l’axe et terminer de visser les 2 dernières vis du moteur sur son support, puis le support sur la caisse.

Montage de l’axe vertical (étape 4)
------------------------------------

Matériel :

  * 2 poulies GT2 20 dents bore 8mm

* Visser les 2 vis en bas du coupleur sur l’arbre du moteur en s’assurant qu’une des vis est en face du méplat de l’axe du moteur et que le bas du coupleur ne repose pas sur le moteur.

.. image :: ./IMG/BrailleRAP-V5.62.jpg
       :align: center

* Enfiler l’axe de 100mm dans les KP08, les poulies (en respectant leurs positions) et le coupleur.

.. image :: ./IMG/BrailleRAP-V5.63.jpg
       :align: center

* Visser les 2 vis en haut du coupleur sur l’axe vertical.

.. image :: ./IMG/BrailleRAP-V5.64.jpg
       :align: center

* Laisser les poulies libres sans les visser sur l'axe. Elles seront vissées quand la courroie sera en place.
* Visser les vis des bagues de serrage des KP08 (2 vis par bague).

.. image :: ./IMG/BrailleRAP-V5.65.jpg
       :align: center

* S’assurer que l’axe tourne aisément et que le moteur n’oscille pas. Le cas échéant, desserrer les vis du moteur et du support sur la caisse pour leur donner du jeu et refaire l’alignement.

Montage de la courroie du chariot bas
--------------------------------------

Matériel :

  * 1 courroie GT2 longueur ± 620mm
  * 2 colliers

* A l’aide d’un collier, attacher la courroie autour de la vis du chariot avec les dents à l’extérieur. **AJOUTER IMAGE**
* Faire passer la courroie dans la poulie libre puis la poulie de l’axe vertical.
* Tendre la courroie en retenant le chariot et fixer la deuxième extrémité de la courroie sur sa vis avec un collier. **AJOUTER IMAGE**
* Finir de tendre la courroie à l'aide de la vis à l'extérieur de la caisse. **AJOUTER IMAGE**

.. Note:: Pour l'instant, ne pas serrer les vis de la poulie sur l'axe.

.. image :: ./IMG/BrailleRAP-V5.66.jpg
       :align: center

Montage de l’axe Y (étape 1)
-----------------------------

Matériel :

  * **Pièce(s) imprimée(s) en 3D** : 2 x ROLL_joint
  * 1 taraud M3
  * 2 joints toriques
  * 2 vis M3-6 sans tête bout pointeau
  * 2 KFL8
  * 4 vis M5-18
  * 4 écrous M5 NYL
  * 4 rondelles M5
  * 1 poulie GT2 20 dents bore 8mm
  * 1 barre lisse Ø 8mm, longueur : 364mm
  * 1 courroie GT2 fermée 200 ou 220 mm (selon le support moteur Y )

* Fixer les KFL8 à gauche sur la caisse avec 2 vis M5-18, 2 rondelles M5 et 2 écrous M5 NYL.

.. image :: ./IMG/BrailleRAP-V5.67.jpg
       :align: center

.. image :: ./IMG/BrailleRAP-V5.68.jpg
       :align: center

* Fixer les KFL8 à droite sur la caisse avec les KFL8_support, 2 vis M5-18, 2 rondelles M5 et les 2 écrous M5 NYL.

.. image :: ./IMG/BrailleRAP-V5.69.jpg
       :align: center

.. image :: ./IMG/BrailleRAP-V5.70.jpg
       :align: center

* Tarauder les 2 ROLL_joint.

.. image :: ./IMG/BrailleRAP-V5.41.jpg
       :align: center

* Mettre les joints toriques dans la gorge des 2 ROLL_joint.

.. image :: ./IMG/BrailleRAP-V5.42.jpg
       :align: center

* Visser les vis M3-5 sans tête en s'assurant qu'elles ne dépassent pas à l'intérieur du trou.

.. image :: ./IMG/BrailleRAP-V5.43.jpg
       :align: center

* Enfiler la barre lisse à mi course par le côté gauche à travers la caisse et le KFL8.
* Dans l’ordre, enfiler la poulie GT2 20 dents bore 8mm, la courroie fermée et les 2 ROLL_joint (attention à la position du joint torique). Mettre la courroie fermée sur la poulie du moteur Y et sur la poulie de l’axe.

.. image :: ./IMG/BrailleRAP-V5.73.jpg
       :align: center

* Enfoncer l’axe dans le KFL8 de droite et le faire traverser pour qu’il dépasse de ±12mm de la caisse.

.. image :: ./IMG/BrailleRAP-V5.74.jpg
       :align: center

* Serrer les vis des bagues des KFL8.

.. image :: ./IMG/BrailleRAP-V5.75.jpg
       :align: center

Montage des molettes
-----------------------------

Matériel :

  * **Pièce(s) imprimée(s) en 3D** : 2 x SCROLL_wheel
  * 2 vis M3-8 sans tête **Michel, on t'a mis des M3-12 sans tête ;)**
  * 2 écrous M3

* Introduire les écrous M3 dans leur logement et y visser les vis M3-8 sans tête.

.. image :: ./IMG/BrailleRAP-V5.71.jpg
       :align: center

* Fixer les molettes sur l'axe en vissant les vis M3-8 sans tête.

.. image :: ./IMG/BrailleRAP-V5.72.jpg
       :align: center

Montage de l’axe Y (étape 2)
-----------------------------

* Faire tourner à la main la poulie du moteur afin que la poulie de l’axe s’aligne verticalement avec la poulie du moteur.

.. image :: ./IMG/BrailleRAP-V5.76.jpg
       :align: center

.. image :: ./IMG/BrailleRAP-V5.76.1.jpg
       :align: center

* Déplacer l’ensemble moteur Y/support le long des trous oblongs sous la caisse afin de tendre la courroie fermée puis serrer les 2 vis.

.. image :: ./IMG/BrailleRAP-V5.77.jpg
       :align: center

* Serrer les 2 vis de la poulie de l'axe.

.. image :: ./IMG/BrailleRAP-V5.78.jpg
       :align: center

* Mettre en place la plaque en CP (sans la coller) afin d’aligner les ROLL_joint avec les trous présents dans la plaque. **AJOUTER IMAGE**
* Quand les ROLL_joint sont bien en place, serrer les vis sans tête. **AJOUTER IMAGE**
* Retirer la plaque de contre plaqué.

Montage du chariot haut (étape 1)
----------------------------------

Matériel :

  * **Pièce(s) imprimée(s) en 3D** : TOP_trolley
  * **Pièce(s) imprimée(s) en 3D** : FEMALE_shape
  * Taraud M3

  * 1 vis sans tête M3-30
  * 1 écrou borgne M3

  * 2 vis M3-12
  * 2 rondelles M3 moyennes
  * 2 vis M3-20
  * 4 écrous M3 NYL

  * 3 IGUS_housing
  * 6 vis M3-12
  * 6 écrous M3 NYL

* Encoller le pas de vis de l'écrou borgne et visser la vis M3-30 sans tête du côté **SANS** emprunte allen.

.. image :: ./IMG/BrailleRAP-V5.79.jpg
       :align: center

* Tarauder la FEMALE_shape au 2/3 en partant du haut.

.. image :: ./IMG/BrailleRAP-V5.80.jpg
       :align: center

* Visser l’ensemble vis M3-30/écrou borgne pour le laisser dépasser ± 0,5mm.

.. image :: ./IMG/BrailleRAP-V5.81.jpg
       :align: center

* Assembler la FEMALE_shape sur le TOP_trolley avec les vis M3-12, les rondelles M3 et les écrous M3 NYL en laissant du jeu.

.. image :: ./IMG/BrailleRAP-V5.82.jpg
       :align: center

.. image :: ./IMG/BrailleRAP-V5.83.jpg
       :align: center

* Positionner les IGUS dans les IGUS_housing en respectant le côté du blocage puis visser sur le chariot avec le M3-12 et les écrous M3 NYL.

.. image :: ./IMG/BrailleRAP-V5.88.jpg
       :align: center

.. image :: ./IMG/BrailleRAP-V5.84.jpg
       :align: center

.. image :: ./IMG/BrailleRAP-V5.85.jpg
       :align: center

* Monter les vis M3-20 et les écrous M3.

.. image :: ./IMG/BrailleRAP-V5.87.jpg
       :align: center

.. image :: ./IMG/BrailleRAP-V5.86.jpg
       :align: center

Montage du chariot haut (étape 2)
----------------------------------

Matériel :

  * 2 barres lisses Ø 8mm, longueur : 330mm

* Enfiler les barres à mi-course par l’extérieur de la caisse.

.. image :: ./IMG/BrailleRAP-V5.89.jpg
       :align: center

* Enfiler le chariot bas sur les barres lisses.

.. image :: ./IMG/BrailleRAP-V5.90.jpg
       :align: center

* Terminer d’enfiler les barres.

.. Note:: La tranche du bois doit rester apparente.

.. image :: ./IMG/BrailleRAP-V5.91.jpg
       :align: center

* Serrer les vis des supports d’axes sur la caisse à gauche et à droite.

.. image :: ./IMG/BrailleRAP-V5.92.jpg
       :align: center

* Visser les vis sans tête des supports des axes à gauche et à droite.

.. image :: ./IMG/BrailleRAP-V5.93.jpg
       :align: center

Pose de la courroie du chariot haut
--------------------------------------

Montage des lève-papiers sur la plaque
----------------------------------------

Matériel :

  * PAPER_support (contre-plaqué de 5mm découpé au laser).
  * **Pièce(s) imprimée(s) en 3D** : 2 PAPER_raiser
  * 4 vis à bois 3-10 tête fraisée **Michel, on n'en avait plus ;(E**

* Visser les 2 PAPER_raiser sur la plaque par en dessous avec les vis à bois.

.. image :: ./IMG/BrailleRAP-V5.95.jpg
       :align: center

Collage de la plaque repose papier
-------------------------------------

Matériel :

  * PAPER_support (contre-plaqué de 5mm découpé au laser).
  * **Pièce(s) imprimée(s) en 3D** : 2 PAPER_raiser

* Encoller les encoches qui vont être en contact. Introduire la plaque par l'avant et la maintenir fermement avec du ruban adhésif pendant le temps de séchage.

.. image :: ./IMG/BrailleRAP-V5.96.jpg
       :align: center

.. image :: ./IMG/BrailleRAP-V5.97.jpg
       :align: center

.. image :: ./IMG/BrailleRAP-V5.98.jpg
       :align: center

Montage des guide-papiers sur la plaque
----------------------------------------

Matériel :

  * **Pièce(s) imprimée(s) en 3D** : PAPER_GUIDE_left_1
  * **Pièce(s) imprimée(s) en 3D** : PAPER_GUIDE_left_2
  * **Pièce(s) imprimée(s) en 3D** : PAPER_GUIDE_right_1
  * **Pièce(s) imprimée(s) en 3D** : PAPER_GUIDE_right_2
  * 4 vis M3-16
  * 4 écrous M3 NYL

.. NOTE:: Pour plus de clarté, nous avons isolé la partie concernée.

.. image :: ./IMG/BrailleRAP-V5.102.jpg
       :align: center

.. image :: ./IMG/BrailleRAP-V5.101.jpg
       :align: center

* Assembler les guide-papiers sur la plaque avec les vis M3-16 et les écrous M3 NYL.

.. image :: ./IMG/BrailleRAP-V5.99.jpg
       :align: center

* Vous devez obtenir une vue du dessus comme celle ci :

.. image :: ./IMG/BrailleRAP-V5.100.jpg
       :align: center

* Centrer les rouleaux dans les trous de la plaque et visser les vis sans tête jusqu'à ce que les rouleaux soient bien solidaires de l'axe.

.. image :: ./IMG/BrailleRAP-V5.103.jpg
       :align: center

Montage des presse-papiers (étape 1) :
----------------------------------------

Matériel :

  * **Pièce(s) imprimée(s) en 3D** : 2 CLIPBOARD
  * **Pièce(s) imprimée(s) en 3D** : 2 CLIPBOARD_wheel
  * 2 vis M3-20
  * 4 écrous M3 NYL

* Assembler les CLIPBOARD avec CLIPBOARD_wheel à l'aide des vis M3-20 et des écrous M3 NYL. Serrer la vis en laissant la possibilité à la roue de tourner.

.. image :: ./IMG/BrailleRAP-V5.113.jpg
       :align: center

.. image :: ./IMG/BrailleRAP-V5.114.jpg
       :align: center

Montage des presse-papiers (étape 2) :
----------------------------------------

Matériel :

  * 2 CLIPBOARD montés à l'étape 1
  * 4 vis M3-14
  * 4 rondelles M3 moyennes
  * 4 écrous M3 NYL

.. NOTE:: Les trous oblongs dans les pièces imprimées permettent de régler la pression des CLIPBOARD sur le papier.

.. image :: ./IMG/BrailleRAP-V5.104.jpg
       :align: center

.. image :: ./IMG/BrailleRAP-V5.105.jpg
       :align: center

Montage du fin de course Y 
------------------------------

Matériel :

  * **Pièce(s) imprimée(s) en 3D** : SWITCH_Y_support
  * 2 vis M3-14
  * 2 rondelles M3 moyennes
  * 2 écrous M3 NYL
  * 1 interrupteur fin de course à lamelle
  * 2 vis M2.5-14
  * 2 écrous M2.5 NYL

.. NOTE:: L'interrupteur fin de course à lamelle devra être câblé avant d'être monté sur son support (non représenté).

* Assembler l'interrupteur fin de course et le SWITCH_Y_support à l'aide des vis M2.5-14 et des écrous M2.5 NYL.

.. image :: ./IMG/BrailleRAP-V5.106.jpg
       :align: center

.. image :: ./IMG/BrailleRAP-V5.107.jpg
       :align: center

.. NOTE:: La position de l'interrupteur dans les trous oblongs sera réglée à la fin de l'assemblage et les vis serrées.

* Assembler l'ensemble interrupteur fin de course et le SWITCH_Y_support sur la caisse à l'aide des vis M3-14, des rondelles M3 et des écrous M3 NYL.

.. image :: ./IMG/BrailleRAP-V5.108.jpg
       :align: center

.. image :: ./IMG/BrailleRAP-V5.109.jpg
       :align: center

Fixation des clips sur le couvercle
--------------------------------------

Matériel :

  * **Pièce(s) imprimée(s) en 3D** : 2 LID_LOCK
  * 4 vis M3-14
  * 4 écrous M3 NYL

* Assembler les 2 LID_LOCK sur le couvercle à l'aide des vis M3-14, des rondelles M3 et des écrous M3 NYL.

.. image :: ./IMG/BrailleRAP-V5.110.jpg
       :align: center

.. image :: ./IMG/BrailleRAP-V5.111.jpg
       :align: center

Fixation de la plaque pour l'embase de l'alimentation
-------------------------------------------------------

Matériel :

  * **Pièce(s) imprimée(s) en 3D** : POWER_plate
  * 4 vis M3-14
  * 4 écrous M3 NYL

*  **AJOUTER IMAGE**

Montage de la carte électronique sur la caisse
-----------------------------------------------

Matériel :

  * Carte MKS GEN 1.4
  * 4 entretoises M3-10 **Michel, nous allons te les envoyer dès qu'on les reçoit**
  * 4 rondelles M3 moyennes
  * 8 vis M3-10

* Assembler les 4 entretoises sur la carte.  **AJOUTER IMAGE**
* Assembler la carte sur la caisse.  **AJOUTER IMAGE**

Pose des drivers sur la carte électronique
-------------------------------------------

Matériel :

  * Carte MKS GEN 1.4
  * 2 Drivers DRV8825
  * 6 cavaliers

* Si la carte ne vous est pas fournie déjà équipée de cavaliers, en mettre aux emplacements des drivers des moteurs X et Y. **AJOUTER IMAGE**
* Enfoncer les drivers dans leurs emplacements.  **AJOUTER IMAGE**

Raccordement des moteurs à la carte
------------------------------------

* à faire

Câblage de l’électro-aimant
----------------------------

* à faire

Câblage des interrupteurs fin de course
----------------------------------------

* à faire

Alignement vertical des deux chariots
--------------------------------------

* à faire

* Serrer les poulies sur l’axe vertical. **AJOUTER IMAGE**

Alignement horizontal de l'emprunte du chariot haut
----------------------------------------------------

A ne pas oublier

* Serrer la vis du endstop X

Réglage de la profondeur du point
----------------------------------------------------

* Selon le matériau que vous utiliserez (papier, plastique, aluminium de canette), vous devrez régler la hauteur de l'emprunte du chariot haut à l'aide de l'écrou borgne **à développer avec des exemples**

.. image :: ./IMG/BrailleRAP-V5.112.jpg
       :align: center

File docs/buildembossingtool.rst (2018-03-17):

Building the embossing tool
===========================

Material
--------

The embossing tool is made of an M3 screw, machined with a dremel like tool.

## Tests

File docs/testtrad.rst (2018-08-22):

Test de traduction avec outils sphinx
=====================================

est ce que 'RTFD'genere correctement les fichiers .po ?

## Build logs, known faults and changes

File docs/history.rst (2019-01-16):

Historique du projet
==================================

Le commencement
---------------

En 2016 l'association \*MyHumanKit\* organise en collaboration avec \*Airbus Industries\* un hackaton appelé Fabrikarium. 

Pendant le Fabrikarium plusieurs travaux ont été réalisés pour modifier des imprimantes 3D afin d'embosser du \**Braille\** sur du papier 160g, 

Le projet s'appelait `BrailleRap <https://github.com/arthursw/BrailleRap/blob/master/Documentation/documentation-en.md>`_.

Dans l'equipe BrailleRAP-SP nous pensions que ces travaux êtaient une démonstration de faisabilité, 
mais qu'il fallait mettre au point une machine spécialisée facile à reproduire.

OpenBraille
-----------
En 2017 Carlos Campos démarre le projet OpenBraille et construit une embosseuse braille à partir de pièces d'imprimante recyclées. 

Le projet démontre qu'il est possible de déplacer une feuille de papier avec suffisamment de précision dans une embosseuse braille. 

BrailleRap-SP
-------------
En Janvier 2018, nous avons commencé avec quelques rails linéaires, des moteurs Nema et des pièces imprimées pour essayer de réaliser une embosseuse Braille. Quelques essais plus tard, nous avons commencé à montrer des exemples de textes embossés en Braille, et tout le monde était très enthousiastes. Le projet BrailleRAP-SP était né.  

.. raw:: html

    <div style="position: relative; padding-bottom: 56.25%; height: 0; overflow: hidden; max-width: 100%; height: auto;">
	    <iframe width="560" height="315" src="https://www.youtube.com/embed/IYYWQi-H3YY" frameborder="0" allow="autoplay; encrypted-media" allowfullscreen style="position: absolute; top: 0; left: 0; width: 100%; height: 100%;"> </iframe> 
    </div>

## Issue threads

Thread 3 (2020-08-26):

Information about the Marlin Braille compilation

juliano-lopes, 2020-08-26:
Hello,

to try to build Marlin Braille application, an error is displayed:

In file included from sketch\Marlin_main.cpp:314:0:
sketch\endstop_interrupts.h: In function 'void setup_endstop_interrupts()':
endstop_interrupts.h:148:7: error: non-constant condition for static assertion
       static_assert(digitalPinToPCICR(Y_MIN_PIN) != NULL, "Y_MIN_PIN is not interrupt-capable");
       ^~~~~~~~~~~~~
In file included from sketch\Marlin_main.cpp:314:0:
endstop_interrupts.h:54:57: error: reinterpret_cast from integer to pointer
                                     WITHIN(p, 62, 69) ? &PCICR : (uint8_t*)0 )
                                                         ^
sketch\endstop_interrupts.h:148:21: note: in expansion of macro 'digitalPinToPCICR'
       static_assert(digitalPinToPCICR(Y_MIN_PIN) != NULL, "Y_MIN_PIN is not interrupt-capable");
                     ^~~~~~~~~~~~~~~~~
exit status 1
non-constant condition for static assertion

It's been used the arduino mega.
I'd like to know if you can helpe me, please. I couldn't find how I can build the application on the documentation.

Best regards.

crocsg, 2020-08-27:
Hello Julianos
i just check the compilation on Arduino IDE 1.8.12, and i have the same error. I gave a few try with Arduino IDE 1.8.9 and i don't have the issue. This is maybe a quick workaround if you can get Arduino IDE 1.8.9.  I will have a deeper look in the next few days and deliver a new release.

Best Regards

crocsg, 2020-09-04:
Hello Julianos
i just delivered a patch in the master branch that work well with Arduino 1.8.12

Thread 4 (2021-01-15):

purchasing brailleRap embossers and their replacement parts

joshknnd1982, 2021-01-15:
I am a blind adult consumer and a stay-at-home parent with a sighted child doing remote learning in school because of coronavirus. I just bought a braille Buddy embosser for $1495 united states dollars from www.irie-at.com It is the cheapest on the market so far. If it ever breaks though, I have to send it back for repair. I cannot just purchase new styluses, install them and keep on printing. viewPlus embosser parts cannot be purchased by individual consumers like myself. So could you please partner with viewPlus or irie-at and modify this embosser so it works with the Tiger software Suite and uses regular windows and linux and mac printer drivers, and also please work with viewPlus or irie-at or orbit Research, in order to bring a modified tiger software-suite-compatible-version of the brailleRap embosser at an affordable price such as $800 to $995 or $1095 United-states-dollars, for consumers to purchase. $1495 for the braille buddy is still a bit too much money for a consumer braille printer I think. I just want to buy one of these brailleRap printers from a company, have it shipped to my house, plug it into my computer, put paper in it, install some windows, mac, or linux cups printer drivers, maybe an addon for word or a universal translator sitting in the system tray using liblouis, open word, excel, microsoft-paint, or any application, open a document, or a picture, graph, chart, hit print, choose the viewPlus brailleRap, and hit print. or go into printer properties, put brailleRap into legacy mode and then use it with free brailleBlaster translator. So please please partner with some company and sell these embossers at an affordable price. thanks.

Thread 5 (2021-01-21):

preparing to market and manufacture braillerap embosser mass distribution and sales

joshknnd1982, 2021-01-21:
I got this email from a manufacturing company who seems willing to manufacture this embosser for distribution and sales through a company or distributor such as Orbit Research, American Printing House for the Blind, or Maxiaids...
----------------------------------------
Josh,

I hope all is well. Michael passed this ticket to my desk. It looks like a great project, however I do not see a PCB in the details noted on your web page. MacroFab does not do any assembly where we do not first build the PCB. Please let me know if I am missing something as if this project does require a PCB, we can certainly help.

Regards,

Jerry

Jerry McDaniel Director - Customer Success
MacroFab, Inc.
O: 713.300.2591 x713
M: 713-384-9911

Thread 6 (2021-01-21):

manufacturing braillerap for sale and mass distribution revisited

joshknnd1982, 2021-01-21:
I got this email from Jerry of MacroFab. he has more questions about manufacturing. Please get back to me on this so I can either sell braillerap or hand braillerap off to american printing house of the blind www.aph.org ... or orbit research for manufacture and sale, www.orbitresearch.com ... thanks ...
------------------------------------------------------------

Josh,

Thanks for the update however I am not certain I understand your note. Does your braillerap.com project require the assembly of a PCB? If so, please let me know so that I can take a look at the files you have to see if they are suitable for our platform.

Regards,

Jerry

Jerry McDaniel Director - Customer Success
MacroFab, Inc.
O: 713.300.2591 x713
M: 713-384-9911
MacroFab Podcast | Twitter | Slack

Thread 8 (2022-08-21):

STL Missing

maumontel, 2022-08-21:
Where do I find these printed parts from paper guide or it is not necessary anymore?

The STL folder has only PAPER_GUIDE_left.stl and PAPER_GUIDE_right.stl and the montage manual says
Pièce(s) imprimée(s) en 3D : PAPER_GUIDE_left_1
Pièce(s) imprimée(s) en 3D : PAPER_GUIDE_left_2
Pièce(s) imprimée(s) en 3D : PAPER_GUIDE_right_1
Pièce(s) imprimée(s) en 3D : PAPER_GUIDE_right_2

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

Thanks,
Mauricio

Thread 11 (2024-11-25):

CAD Files

asolino, 2024-11-25:
Hey folks.. great project. Would love to build a printer for my daughter.
Is there any chance to get the CAD files for the STLs? I might need to change some of them due to BOM availability in my country. Thanks!

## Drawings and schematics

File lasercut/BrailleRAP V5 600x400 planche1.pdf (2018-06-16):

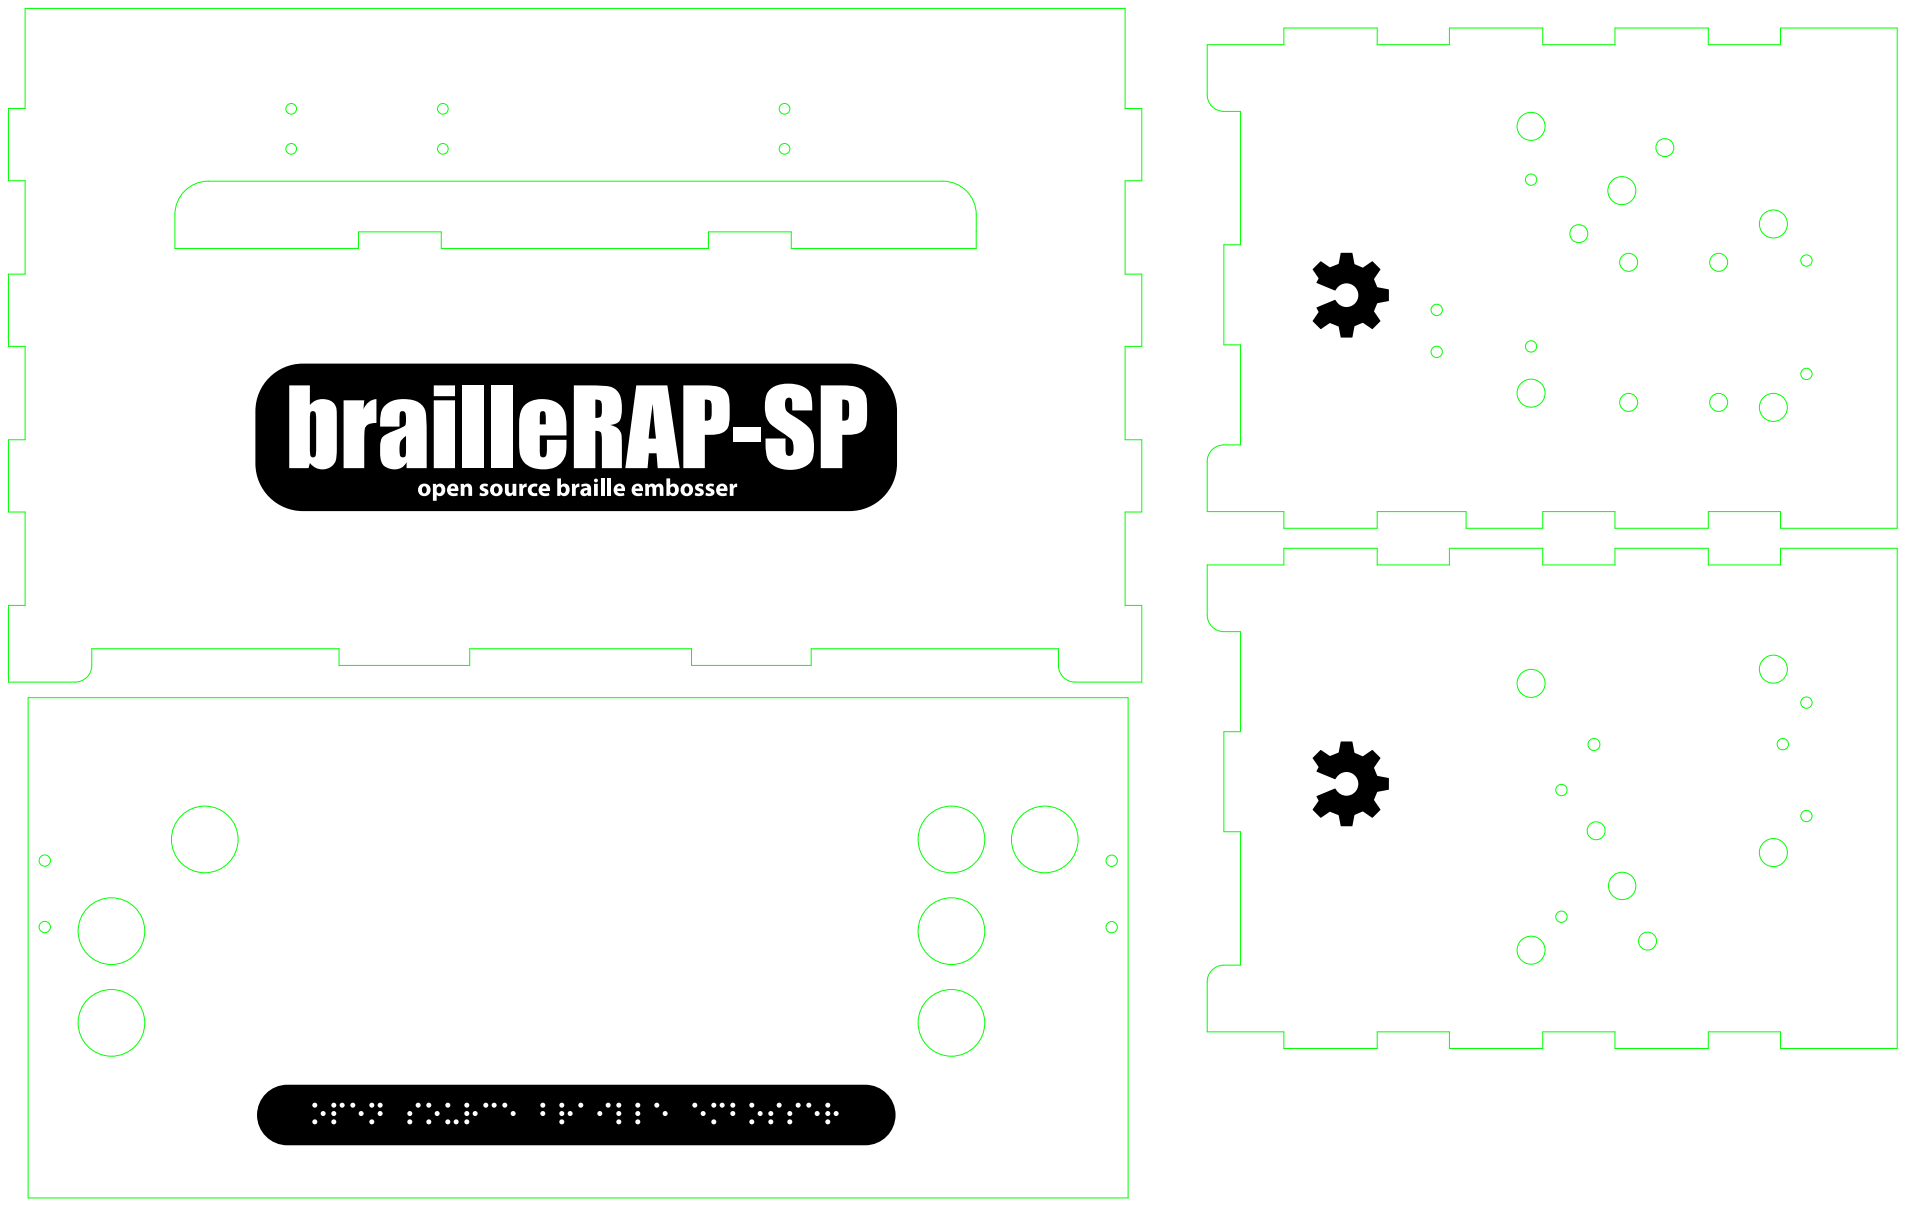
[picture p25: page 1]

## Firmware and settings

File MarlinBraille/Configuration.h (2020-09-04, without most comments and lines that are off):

#define CONFIGURATION_H
#define CONFIGURATION_H_VERSION 010107
#define STRING_CONFIG_H_AUTHOR "BrailleRap marlin" // Who made the changes.
#define SHOW_BOOTSCREEN
#define STRING_SPLASH_LINE1 SHORT_BUILD_VERSION // will be shown during bootup in line 1
#define STRING_SPLASH_LINE2 WEBSITE_URL         // will be shown during bootup in line 2
#define SERIAL_PORT 0
#define BAUDRATE 250000
  #define MOTHERBOARD BOARD_RAMPS_14_SF
#define CUSTOM_MACHINE_NAME "Braille RAP"
#define SPINDLE_LASER_ENABLE
#define SPINDLE_LASER_ENABLE_PIN  RAMPS_D8_PIN      // !!! sortie BED MOSFET
#define SPINDLE_LASER_PWM_PIN     RAMPS_D10_PIN     // !!! sortie E0 MOSFET
#define SPINDLE_DIR_PIN           5                 // pin servo
#define PAPER_LOADING_HOME_Y 1 // homing Y load paper, you mut use YMIN endstop
#define EXTRUDERS 1
#define DEFAULT_NOMINAL_FILAMENT_DIA 3.0
#define POWER_SUPPLY 0
#define TEMP_SENSOR_0 1
#define TEMP_SENSOR_1 0
#define TEMP_SENSOR_2 0
#define TEMP_SENSOR_3 0
#define TEMP_SENSOR_4 0
#define TEMP_SENSOR_BED 0
#define DUMMY_THERMISTOR_998_VALUE 25
#define DUMMY_THERMISTOR_999_VALUE 100
#define MAX_REDUNDANT_TEMP_SENSOR_DIFF 10
#define TEMP_RESIDENCY_TIME 10  // (seconds)
#define TEMP_HYSTERESIS 3       // (degC) range of +/- temperatures considered "close" to the target one
#define TEMP_WINDOW     1       // (degC) Window around target to start the residency timer x degC early.
#define TEMP_BED_RESIDENCY_TIME 10  // (seconds)
#define TEMP_BED_HYSTERESIS 3       // (degC) range of +/- temperatures considered "close" to the target one
#define TEMP_BED_WINDOW     1       // (degC) Window around target to start the residency timer x degC early.
#define HEATER_0_MINTEMP 5
#define HEATER_1_MINTEMP 5
#define HEATER_2_MINTEMP 5
#define HEATER_3_MINTEMP 5
#define HEATER_4_MINTEMP 5
#define BED_MINTEMP 5
#define HEATER_0_MAXTEMP 275
#define HEATER_1_MAXTEMP 275
#define HEATER_2_MAXTEMP 275
#define HEATER_3_MAXTEMP 275
#define HEATER_4_MAXTEMP 275
#define BED_MAXTEMP 150
#define PIDTEMP
#define BANG_MAX 255     // Limits current to nozzle while in bang-bang mode; 255=full current
#define PID_MAX BANG_MAX // Limits current to nozzle while PID is active (see PID_FUNCTIONAL_RANGE below); 255=full current
#define PID_K1 0.95      // Smoothing factor within the PID
  #define PID_FUNCTIONAL_RANGE 10 // If the temperature difference between the target temperature and the actual temperature
  #define  DEFAULT_Kp 22.2
  #define  DEFAULT_Ki 1.08
  #define  DEFAULT_Kd 114
#define MAX_BED_POWER 255 // limits duty cycle to bed; 255=full current
#define PREVENT_COLD_EXTRUSION
#define EXTRUDE_MINTEMP 170
#define PREVENT_LENGTHY_EXTRUDE
#define EXTRUDE_MAXLENGTH 200
#define THERMAL_PROTECTION_HOTENDS // Enable thermal protection for all extruders
#define THERMAL_PROTECTION_BED     // Enable thermal protection for the heated bed
#define USE_XMIN_PLUG
#define USE_YMIN_PLUG
#define USE_ZMIN_PLUG
#define ENDSTOPPULLUPS // Comment this out (using // at the start of the line) to disable the endstop pullup resistors
#define X_MIN_ENDSTOP_INVERTING false // set to true to invert the logic of the endstop.
#define Y_MIN_ENDSTOP_INVERTING false // set to true to invert the logic of the endstop.
#define Z_MIN_ENDSTOP_INVERTING false // set to true to invert the logic of the endstop.
#define X_MAX_ENDSTOP_INVERTING false // set to true to invert the logic of the endstop.
#define Y_MAX_ENDSTOP_INVERTING false // set to true to invert the logic of the endstop.
#define Z_MAX_ENDSTOP_INVERTING false // set to true to invert the logic of the endstop.
#define Z_MIN_PROBE_ENDSTOP_INVERTING false // set to true to invert the logic of the probe.
#define DEFAULT_AXIS_STEPS_PER_UNIT   { 80 * 2, 87, 4000, 500 } // pololu 32 microstep with big roll
#define DEFAULT_MAX_FEEDRATE          { 300, 300, 5, 25 }
#define DEFAULT_MAX_ACCELERATION      { 1500, 1500, 100, 10000 }
#define DEFAULT_ACCELERATION          1500    // X, Y, Z and E acceleration for printing moves
#define DEFAULT_RETRACT_ACCELERATION  1500    // E acceleration for retracts
#define DEFAULT_TRAVEL_ACCELERATION   1500    // X, Y, Z acceleration for travel (non printing) moves
#define DEFAULT_XJERK                 5.0
#define DEFAULT_YJERK                 5.0
#define DEFAULT_ZJERK                  0.3
#define DEFAULT_EJERK                  5.0
#define Z_MIN_PROBE_USES_Z_MIN_ENDSTOP_PIN
#define X_PROBE_OFFSET_FROM_EXTRUDER 10  // X offset: -left  +right  [of the nozzle]
#define Y_PROBE_OFFSET_FROM_EXTRUDER 10  // Y offset: -front +behind [the nozzle]
#define Z_PROBE_OFFSET_FROM_EXTRUDER 0   // Z offset: -below +above  [the nozzle]
#define XY_PROBE_SPEED 8000
#define Z_PROBE_SPEED_FAST HOMING_FEEDRATE_Z
#define Z_PROBE_SPEED_SLOW (Z_PROBE_SPEED_FAST / 2)
#define MULTIPLE_PROBING 2
#define Z_CLEARANCE_DEPLOY_PROBE   10 // Z Clearance for Deploy/Stow
#define Z_CLEARANCE_BETWEEN_PROBES  5 // Z Clearance between probe points
#define Z_PROBE_OFFSET_RANGE_MIN -20
#define Z_PROBE_OFFSET_RANGE_MAX 20
#define X_ENABLE_ON 0
#define Y_ENABLE_ON 0
#define Z_ENABLE_ON 0
#define E_ENABLE_ON 0 // For all extruders
#define DISABLE_X false
#define DISABLE_Y false
#define DISABLE_Z false
#define DISABLE_E false // For all extruders
#define DISABLE_INACTIVE_EXTRUDER true // Keep only the active extruder enabled.
#define INVERT_X_DIR false
#define INVERT_Y_DIR false
#define INVERT_Z_DIR false
#define INVERT_E0_DIR false
#define INVERT_E1_DIR false
#define INVERT_E2_DIR false
#define INVERT_E3_DIR false
#define INVERT_E4_DIR false
#define X_HOME_DIR -1
#define Y_HOME_DIR 1
#define Z_HOME_DIR -1
#define X_BED_SIZE 240
#define Y_BED_SIZE 600
#define X_MIN_POS 0
#define Y_MIN_POS 0
#define Z_MIN_POS 0
#define X_MAX_POS X_BED_SIZE
#define Y_MAX_POS Y_BED_SIZE
#define Z_MAX_POS 200
#define MIN_SOFTWARE_ENDSTOPS
  #define MIN_SOFTWARE_ENDSTOP_X
  #define MIN_SOFTWARE_ENDSTOP_Y
  #define MIN_SOFTWARE_ENDSTOP_Z
#define MAX_SOFTWARE_ENDSTOPS
  #define MAX_SOFTWARE_ENDSTOP_X
  #define MAX_SOFTWARE_ENDSTOP_Y
  #define MAX_SOFTWARE_ENDSTOP_Z
#define MANUAL_Y_HOME_POS -20
#define Z_SAFE_HOMING
  #define Z_SAFE_HOMING_X_POINT ((X_BED_SIZE) / 2)    // X point for Z homing when homing all axes (G28).
  #define Z_SAFE_HOMING_Y_POINT ((Y_BED_SIZE) / 2)    // Y point for Z homing when homing all axes (G28).
#define HOMING_FEEDRATE_XY (20*60*2)
#define HOMING_FEEDRATE_Z  (4*60)
#define EEPROM_SETTINGS // Enable for M500 and M501 commands
#define EEPROM_CHITCHAT   // Give feedback on EEPROM commands. Disable to save PROGMEM.
#define HOST_KEEPALIVE_FEATURE        // Disable this if your host doesn't like keepalive messages
#define DEFAULT_KEEPALIVE_INTERVAL 2  // Number of seconds between "busy" messages. Set with M113.
#define BUSY_WHILE_HEATING            // Some hosts require "busy" messages even during heating
#define PREHEAT_1_TEMP_HOTEND 180
#define PREHEAT_1_TEMP_BED     70
#define PREHEAT_1_FAN_SPEED     0 // Value from 0 to 255
#define PREHEAT_2_TEMP_HOTEND 240
#define PREHEAT_2_TEMP_BED    110
#define PREHEAT_2_FAN_SPEED     0 // Value from 0 to 255
#define PRINTJOB_TIMER_AUTOSTART
#define LCD_LANGUAGE fr
#define DISPLAY_CHARSET_HD44780 JAPANESE
#define SOFT_PWM_SCALE 0
#define SERVO_DELAY { 300 }

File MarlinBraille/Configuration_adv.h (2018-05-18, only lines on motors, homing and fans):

#define E0_AUTO_FAN_PIN -1
#define E1_AUTO_FAN_PIN -1
#define E2_AUTO_FAN_PIN -1
#define E3_AUTO_FAN_PIN -1
#define E4_AUTO_FAN_PIN -1
#define X_HOME_BUMP_MM 5
#define Y_HOME_BUMP_MM 5
#define Z_HOME_BUMP_MM 2
#define HOMING_BUMP_DIVISOR { 2, 2, 4 }  // Re-Bump Speed Divisor (Divides the Homing Feedrate)
#define MICROSTEP_MODES {16,16,16,16,16} // [1,2,4,8,16]
#define DIGIPOT_I2C_MOTOR_CURRENTS { 1.0, 1.0, 1.0, 1.0, 1.0, 1.0, 1.0, 1.0 }  //  AZTEEG_X3_PRO

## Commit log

2018-03-11 added printed parts for test
    [ROULEAU_SUPPORT_TORIQUE.stl, SABOT_MOTEUR_Y.stl, SUPPORT_ELCTRO_AIMANT.stl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]
2018-03-11 Added printed parts url
2018-03-11 Printed parts parameters
2018-03-11 added flyback board
2018-03-11 added flyback schematics
    [flyback.sch]
2018-03-12 update flyback schema
    [flyback.sch]
2018-03-12 update bom page
2018-03-12 update bom
2018-03-12 update fucking bom page
2018-03-12 update marlin doc
2018-03-12 add lasercut
    add lasercut
    [PLANCHE 1.dxf, PLANCHE 2.dxf, PLANCHE 3.dxf]
2018-03-14 Assembling manual
2018-03-14 update assembling manual
2018-03-17 added printed parts
    [ROULEAU_SUPPORT_TORIQUE.stl, charriot haut.stl, galet bas.stl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]
2018-03-18 update doc and bom
    [LOCK_V2.stl]
2018-03-18 update assembling
2018-03-18 move printed parts
2018-03-18 test bom
2018-03-19 update printed parts
    [LOCK_V2.stl, Ymotor_mount.stl, charriot haut.stl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]
2018-03-21 Adding right support assembly
2018-03-21 Adding Right Axis M3 mount image -
2018-03-21 Adding Left Mount images
2018-03-21 images path for left mount assembly
2018-03-21 Lef support assembly images
2018-04-18 added marlin firmware
    [Configuration.h, Configuration_adv.h]
2018-04-18 Added MarliBraille
    [Configuration.h, Configuration_adv.h]
2018-04-18 disable buzzer
    [Configuration.h]
2018-04-21 Y Homing
    [Configuration.h]
2018-04-24 disable debug leveling
    [Configuration.h]
2018-04-24 Passage en Français par défaut. Suppression de Assembling.rst au profit de sa version Fr.
2018-04-24 MAJ du TOC Tree pour cause de passage en Français.
2018-04-24 MAJ TOC Tree pour les licences
2018-04-24 Suppression des anciennes images
2018-04-25 Marlin en francais
2018-04-25 renomme la licence du epo en .txt rst c'est pour la doc !
2018-04-26 Mise a jour diode de roue libre
2018-04-27 printed parts bom
2018-05-14 Ajout des fichiers de traduction pour l'anglais dans Locale/en. Coorection formalisme ReST sur assemblage.rst
2018-05-14 Ajout de custom.css dans _static/css/ et modification du path dans conf.py
2018-05-18 update
    New Y endstop position
    32 microstep
    new joint roll diameter
    [Configuration.h, Configuration_adv.h]
2018-05-27 printed parts update
    [BOTTOM_AXIS_left.stl, BOTTOM_AXIS_right.stl, CLIPBOARD_02.stl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]
2018-06-03 printed parts
    [CLIPBOARD.stl, CLIPBOARD_02.stl, PAPER_GUIDE_left_1.stl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]
2018-06-16 laser cut update
    [PLANCHE 1.dxf, PLANCHE 2.dxf, PLANCHE 3.dxf]
2018-06-28 doc update
    [CLIPBOARD_ROLL.stl, TOP_ROLL_ABS.stl]
2018-06-29 DOC & PARTS
    [3D printed parts excel board.xlsx, CLIPBOARD.stl, CLIPBOARD_ROLL.stl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]
2018-07-11 update step per mm
    [Configuration.h]
2018-07-16 new file: assemblage.po new file: bom.po new file: buildembossingtool.po new file: firstembossingpage.po new file: flybackboard.po new file: history.po new file: index.po new file: licence.po new fil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
2018-07-16 modified: assemblage.po
2018-07-16 deleted: assemblage.po deleted: bom.po deleted: buildembossingtool.po deleted: firstembossingpage.po deleted: flybackboard.po deleted: history.po deleted: index.po deleted: licence.po deleted: marlin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
2018-07-16 modified: assemblage.mo
2018-07-16 modified: assemblage.po new file: bom.mo modified: bom.po new file: buildembossingtool.mo modified: buildembossingtool.po new file: firstembossingpage.mo new file: firstembossingpage.po new file: fly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
2018-07-17 modified: assemblage.mo modified: assemblage.po
2018-07-19 modified: licence.mo modified: licence.po modified: marlin.mo modified: marlin.po
2018-07-29 DOCS & PARTS
    [PAPER_GUIDE_left_1.stl, PAPER_GUIDE_right_1.stl]
2018-08-04 printer parts
    [IGUS_housing.stl]
2018-10-08 printed part
    [IGUS_housing.stl]
2018-10-19 update 8825 step/mm
    [Configuration.h]
2019-01-16 update doc modified: docs/history.rst modified: docs/locale/en/LC_MESSAGES/assemblage.po
2019-01-16 update doc modified: docs/locale/en/LC_MESSAGES/assemblage.mo
2019-01-16 modified: docs/locale/en/LC_MESSAGES/bom.mo
2019-01-16 modified: firstembossingpage.mo modified: firstembossingpage.po modified: marlin.mo modified: marlin.po
2019-02-19 dxf laser cut
    [BrailleRAP V5 600x400 planche1.dxf, BrailleRAP V5 600x400 planche2.dxf]
2020-09-04 disabe endstop interrupt for compiler > 1.6
    [Configuration.h]
2022-04-30 added lasercut file in DXF R14 format
    [BrailleRAP V5 600x400 planche1_r14.dxf, BrailleRAP V5 600x400 planche2-r14.dxf]

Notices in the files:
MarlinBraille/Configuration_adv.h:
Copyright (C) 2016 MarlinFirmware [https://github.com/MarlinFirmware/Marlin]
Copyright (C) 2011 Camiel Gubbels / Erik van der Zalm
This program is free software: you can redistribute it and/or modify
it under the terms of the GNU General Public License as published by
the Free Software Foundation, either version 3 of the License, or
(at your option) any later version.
